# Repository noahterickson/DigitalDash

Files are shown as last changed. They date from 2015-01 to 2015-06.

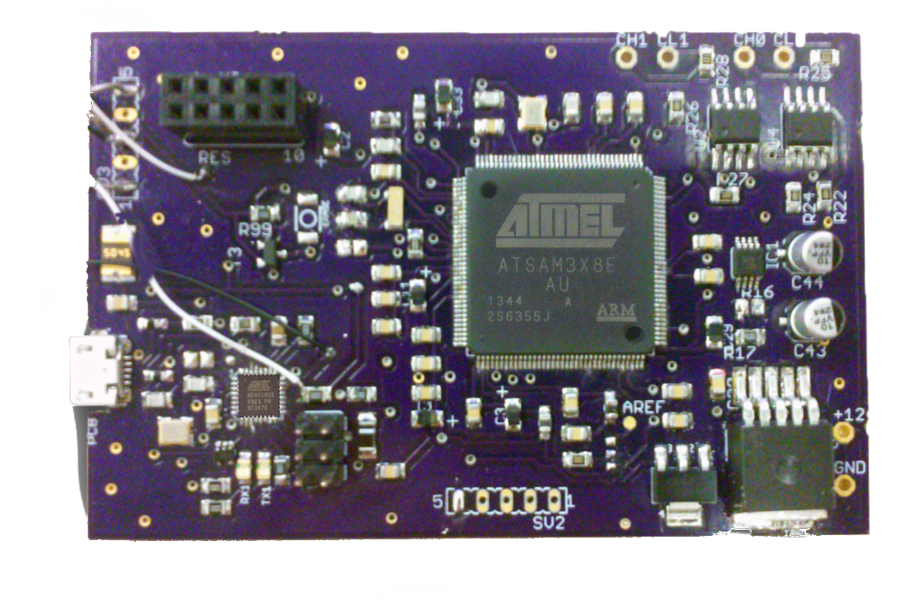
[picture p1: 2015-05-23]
images/Poster/custom.tiff

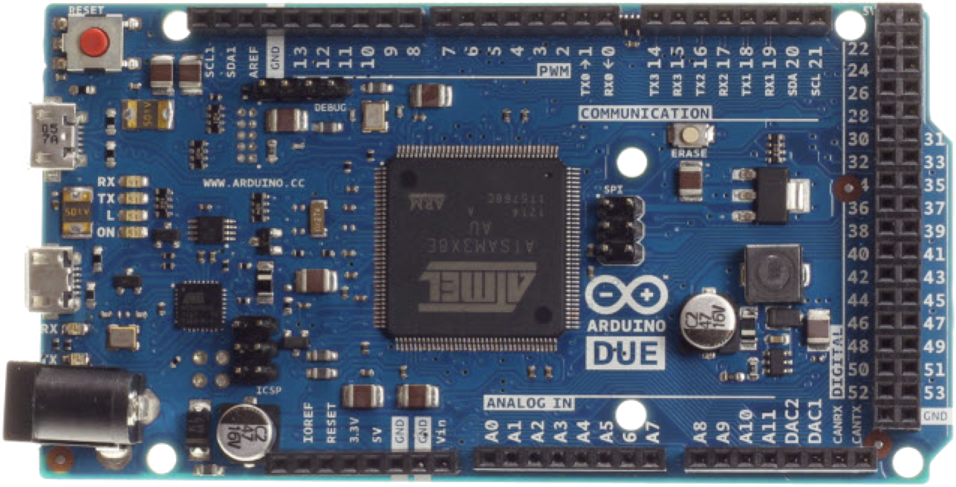
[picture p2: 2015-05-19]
images/Poster/arduino.tiff

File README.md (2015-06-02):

# Digital Dashboard

The digital dashboard project was completed by a group of students at Portland State University for the Electrical and Computer Engineering Capstone program on behalf of the Viking Motorsports team.

The digital dashboard is intended for a Formula SAE electric vehicle and functions as a visual display of information for various systems on the vehicle.

[Check out our wiki](https://github.com/noahterickson/DigitalDash/wiki)

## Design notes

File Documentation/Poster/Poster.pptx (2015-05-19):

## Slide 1

Digital Dash for SAE Electric Race Car
Capstone Team: Noah Erickson, Chad Thueson, Rishal Dass, Jaime Rodriguez, Sean Koppenhafer
Project Sponsor: Michal Podhrasky – Viking Motorsports Team
Capstone Advisor: Dr. Christof Teuscher – Portland State University ECE Department

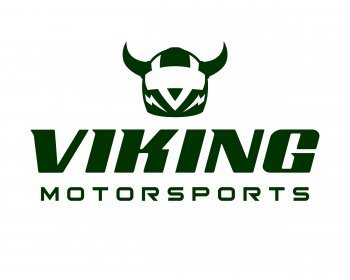
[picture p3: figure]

Prior Work

In the realm of racing each car is designed completely different based on several factors not limited to driver preferences, resources available and technical limitations. A few popular choices for digital dashboards currently exist. The popular Haltech Racepak is not only expensive, but requires the use of Haltech’s standalone ECU to source the data for the dash. Another setup would be a bluetooth adaptor plugged in to an OBDII port on board the car, but would’ve required the use of the OBDII protocol throughout the design of the car.

Implementation

CAN Transceivers

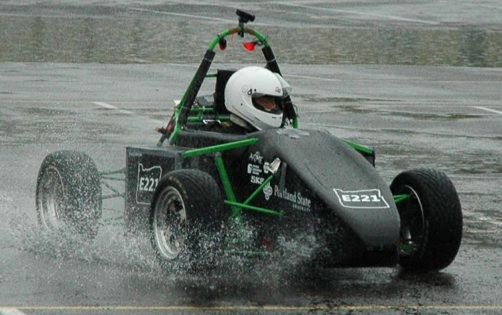
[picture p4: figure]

Microprocessor

Picture of whole unit here

Screen

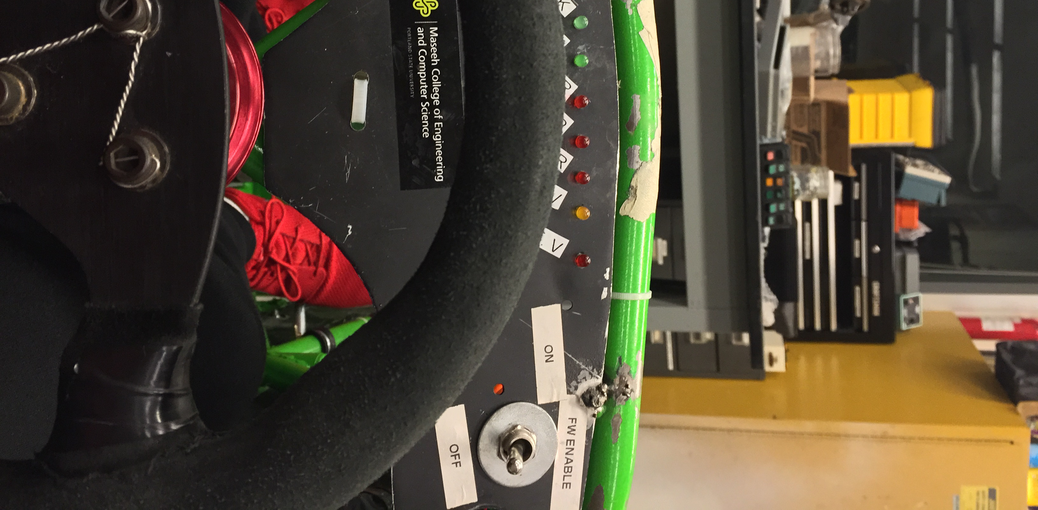
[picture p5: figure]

The software portion of the digital dash was created using the Arduino IDE. In order to interface with the CAN bus and the 4D systems screen the use of two separate Arduino libraries were used. The software sniffs the CAN bus looking for pertinent CAN messages and scales them to their correct values and sends the data to the screen.

The 4D Systems screen came with a useful piece of software to aide the quick creation of GUIs. The screen receives values from the mainboard through a serial connection. The GUI was created to be simple and intuitive. The designed GUI also utilizes the resistive touch capability of the screen in order to flip through a couple different submenus that include further information that a driver might want.

Performance

Oh yeah, it performs.

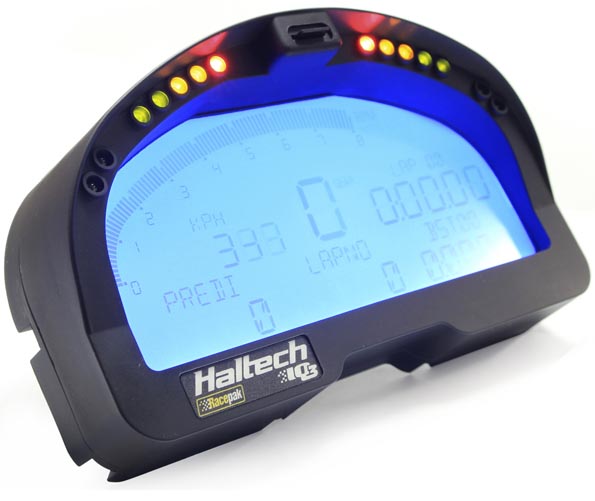
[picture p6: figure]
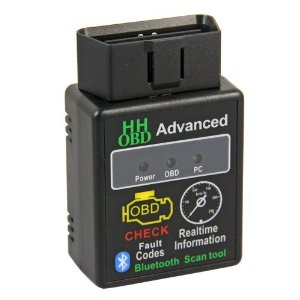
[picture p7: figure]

Hardware

The real estate that the digital dash unit took up on the physical dash needed to be minimal. This requirement dictated two large design choices:
- The 3.5” Display Size
- The custom PCB to cut down size

The entire system was first prototyped using an Arduino Due which was slightly too large for the solution we had in mind.

The screen was slightly smaller than the LCD and the Arduino Due would have a lot of wires plugging into the screen. We wanted our device to be as plug-and-play as possible so we created a custom PCB that would plug directly into the LCD with no “mod wires”.

Software

Screen

Motivation

The increased complexity that high voltage systems introduce onto a racecar require increased diagnostics to keep the car running safely. The Viking Motorsports team had previously used a simple bank of LEDs to indicate problems with mission critical systems. Troubleshooting these problems required the car to be off the track and logged data to be analyzed. With the addition of a digital dash system that reads data in real time from the vehicle control unit the driver could be kept up to date on system functionality either on track or in the pit stop.

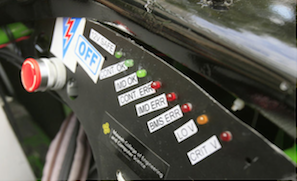
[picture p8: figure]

Picture of LCD screen on Car goes here!!

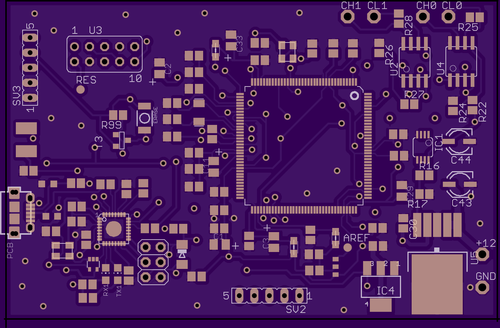
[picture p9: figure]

Further Improvements

- The digital dash could be implemented on the internal combustion car
- Screen size could be maximized to fit the vehicles dash
- The mainboard could be reprinted with the changes made, this would cut down on mod wires, cut traces and test connections
- An improved power supply could be implemented to cut down on power consumption and compatability with a 12V system.
- The enclosure could incorporate a cowl in order to improve readability in direct sunlight

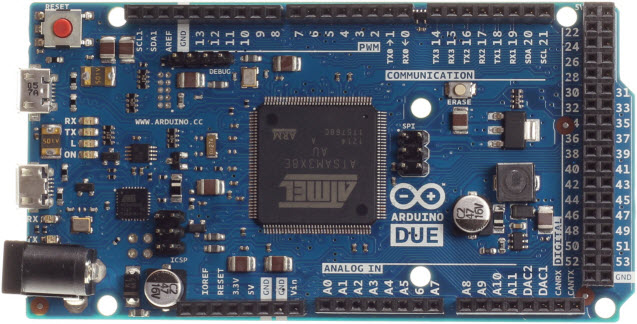
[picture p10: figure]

When it comes to implementing a digital dashboard on a Formula SAE racecar there are three major concerns. The first two concerns are solved by choosing a microprocessor, which was one of the first items we decided on. The microprocessor that drives the digital dashboard must support multiple communications protocols, in this case CAN and serial, and must be fast enough to handle receiving messages on a CAN bus. The 32bit 84MHz ATSAM3X microprocessor, the same microprocessor the Arduino Due uses, fit the bill perfectly with out of the box CAN capability. In addition to the microprocessors fast speeds and CAN capability, the design team could use an Arduino Due as an early prototyping platform while simultaneously designing a custom circuit board to house the ATSAM3X. Another large decision was the screen used since needed to have a high resolution while having a compact size. The high resolution is necessary to draw gauges, icons and bars all on the screen at once while the compact size is required by the layout of the vehicles frame.

Solution

Conclusions

This is objectively the best
digital dash ever created

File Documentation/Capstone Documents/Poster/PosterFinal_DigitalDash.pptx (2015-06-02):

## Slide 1

Digital Dashboard for Formula SAE Electric Racecar
Capstone Team: Noah Erickson, Chad Thueson, Rishal Dass, Jaime Rodriguez, Sean Koppenhafer
Project Sponsor: Michal Podhradsky – Viking Motorsports Team
Capstone Advisor: Dr. Christof Teuscher – Portland State University ECE Department

Acknowledgements: Michal Podhradsky, Dr. Christof Teuscher, Quinn Sullivan and the entire Viking Motorsports Team

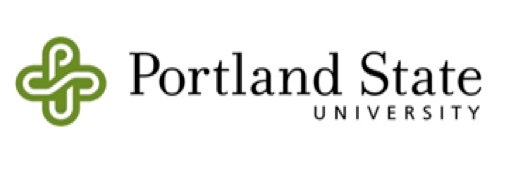
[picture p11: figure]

Abstract

The Viking Motorsports Electrical Vehicle (Figure 1) uses an array of LEDs to indicate problems with mission critical systems. (Figure 2) The increased complexity that high voltage systems introduce into a racecar require increased diagnostics to keep the car running safely and correctly. The driver must have the status of all important subsystems visible to clearly see and determine the vital faults, so they can adjust their driving style as necessary. With an updated dash system detailed information can be displayed in real time from the vehicle control unit. The driver can be kept up to date on system functionality both on track or in the pits.
The solution to display all this critical information is a small 3.5” LCD screen that will receive information from the subsystems of the vehicle and display them in a simple Graphical User Interface. The interface will not only display the warnings and faults like the old LED implementation but will also display useful real time information such as motor torque, battery level and amperage draw of the motor.

Implementation

Figure 4: Digital Dash Block Diagram

Software

The software for the Digital Dashboard was written in the Arduino IDE using the C programming language. In order to interface with the vehicles CAN networks and the 4D systems screen, two libraries provided by the respective distributers were used. The software receives data from the vehicles CAN networks by looking for pertinent messages. Then the messages are interpreted and sent to the screen.

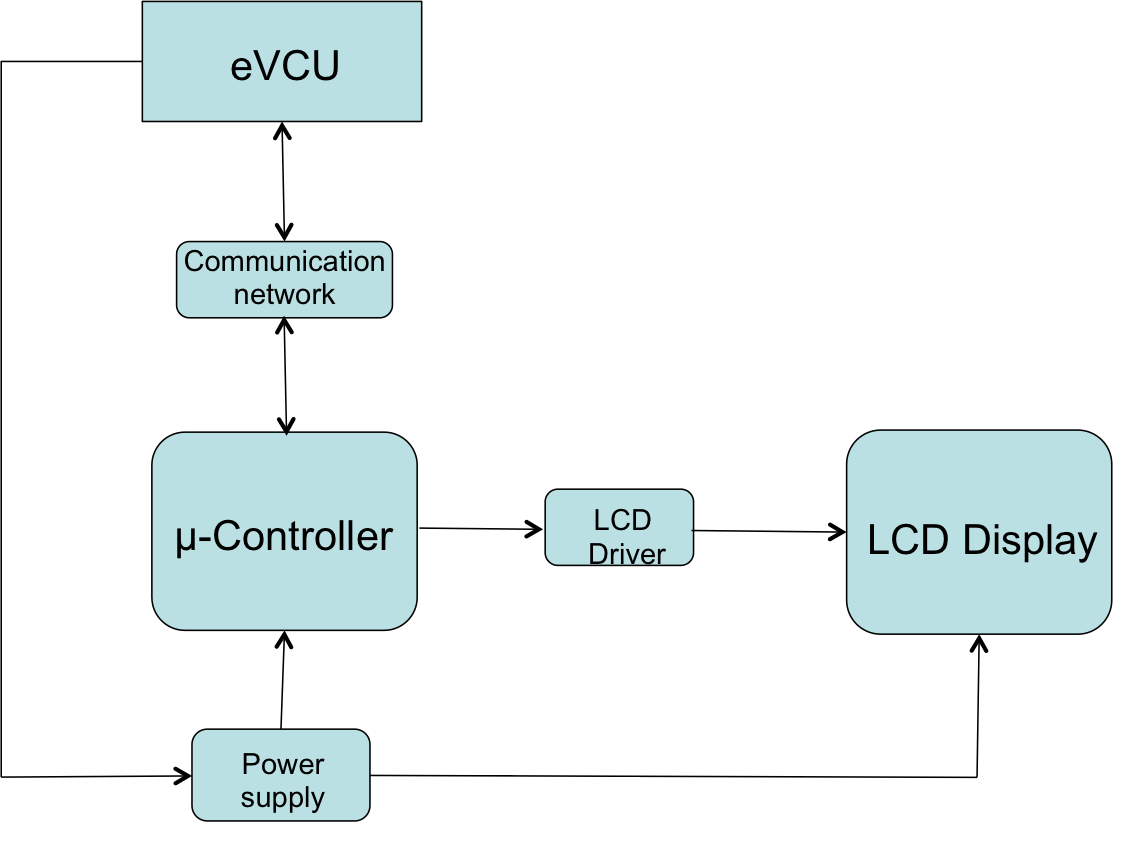
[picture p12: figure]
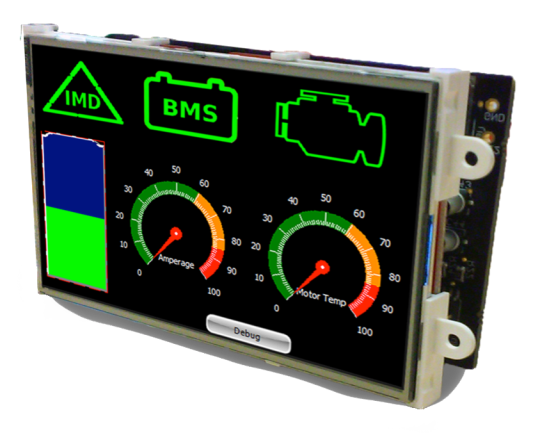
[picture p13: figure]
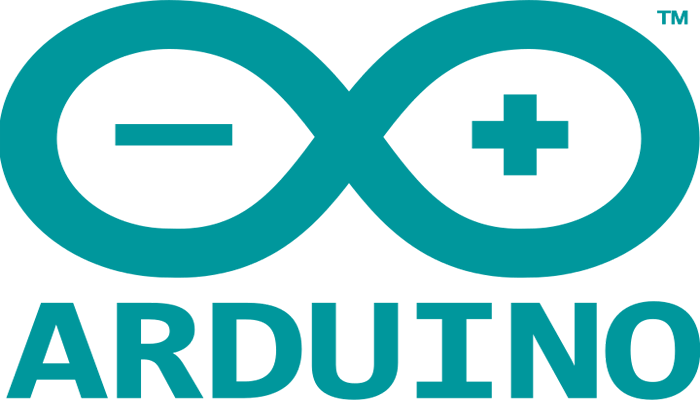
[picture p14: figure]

CAN Network

Programming Circuit

LCD Mating
Header


CAN Inputs

12V Supply

Figure 5: Custom PCB

Testing

For half of the development cycle we were able to use last years car as a test platform. During this time we were able to determine that messages from one of the two CAN networks were successfully being received and interpreted.
In the second half of the development cycle we did not have access to a functioning test vehicle. To determine if the digital dashboard worked, we developed a demo program to send out simulated messages that behaved similarly to the vehicles subsystems.


Figure 1: VMS SAE Electric Vehicle


Figure 2: Current Dash of Electric Vehicle

Hardware

A custom PCB was fabricated to fit in the limited space allocated for the dash in the vehicle. The layout of the board was designed so the control pins of the LCD would connect directly with the header affixed on the board. Our board was created by modifying the existing Arduino Due design. (Figure 5)

LCD DISPLAY

System
Micro Controller

CAN
Network

eVCU
Simulator

Data Input
Controller

Figure 7: Block Diagram for Demo System

Introduction to CAN

The Controller Area Network (CAN) bus is one of several central networking protocols that are used in the automotive industry. Implementing the CAN protocol allows the vehicles subsystems to communicate between each other.

Figure 3: CAN Network Example

The 3.5” screen is touch enabled. It gives us the capability to navigate through multiple screens by way of on screen buttons to view data from different systems. This allows the user to view more detailed information about the vehicles’ respective subsystems. The screen layout was kept as simple as possible to allow the driver to quickly glance at the screen and interpret the data.(Figure 6)

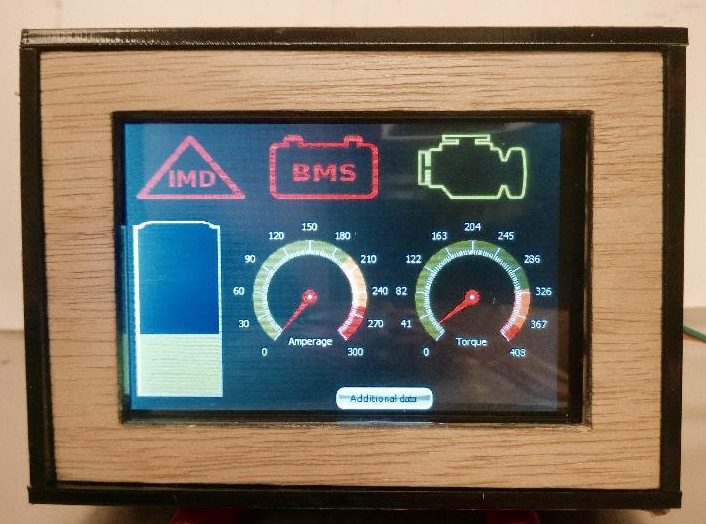
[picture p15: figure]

Figure 6: LCD Displaying Main Screen

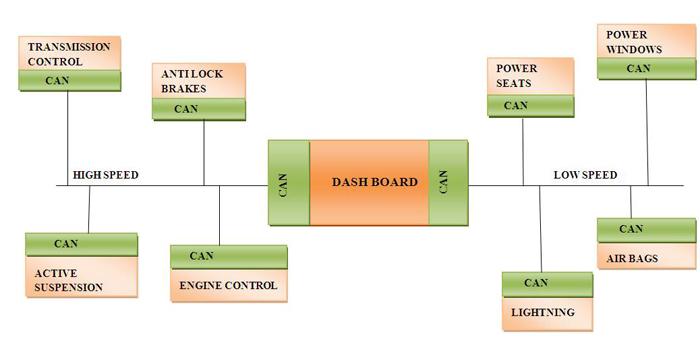
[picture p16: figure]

Conclusion

The digital dashboard performs as intended when simulated with the demo program that we created. Instead of testing all functionally of the screen, the demo program focuses on only the most important functions.
Due to circumstances outside of our control, the digital dashboard has not been officially tested on the electric vehicle but we are confident that it would function correctly.

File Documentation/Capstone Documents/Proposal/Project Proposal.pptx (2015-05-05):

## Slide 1

Sean Koppenhafer, Jaime Rodriguez,
Chad Thueson, Noah Erickson, Rishal Dass

Project Proposal

Digital Dash

Portland State University

Department of Electrical and Computer Engineering (ECE)

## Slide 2

Overview

- Project Overview & Requirements
- Devices Chosen
  - Microcontroller
  - CAN Transceiver
  - LCD Screen
- GUI Layout
- Enclosure
- Budget
- Project Timeline

## Project Overview

- Electric systems add complexity and a traditional LED dash won't suffice
- Drivers must be aware of system faults and warnings
- An LCD Dashboard must be created to accommodate additional electrical systems

Formula SAE Electric Car

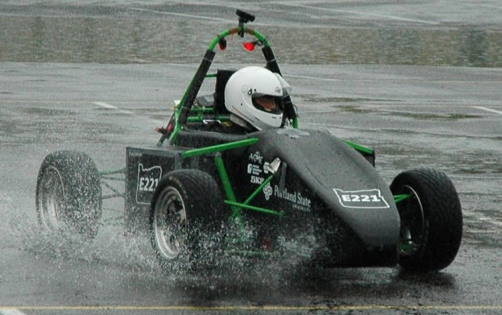
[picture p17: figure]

Current Traditional LED Dash

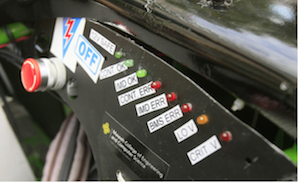
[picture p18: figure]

## Project Requirements

- Budget: $500
- Timeline: March 2015
- The display gather information from the CAN-bus and display it in a simple LCD GUI
- Deliverables
  - One functional Unit
  - Well Documented Code
  - Professional Documentation
  - User Manual

## Design Constraints

- Choose most suitable LCD display
- Design the communication interface with VCU
- Develop GUI
- Design waterproof casing for the display
- Physical space on dash is limited

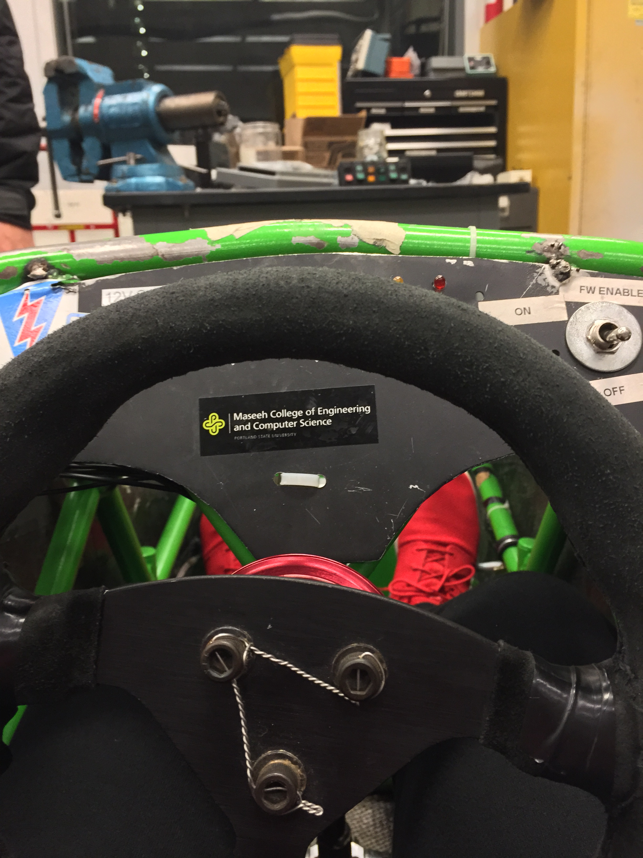
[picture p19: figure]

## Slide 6

Devices Chosen

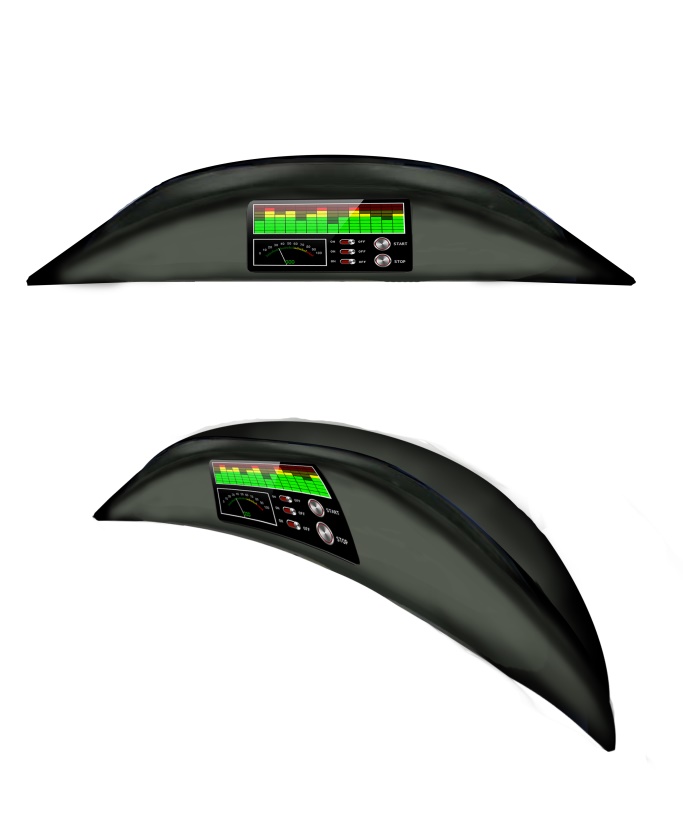
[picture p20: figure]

- CAN Protocol for data acquisition with serial to LCD
- AT90CAN Atmel
- AMS-42700 On Semiconductor
- uLCD-35DT 4D systems

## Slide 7

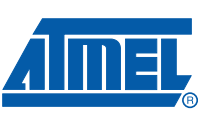
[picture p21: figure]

Microcontrollers

| Cost | Fab Board | CAN Controller | CAN Library | SPI, I2C, UART, etc
Atmega 328 | ~$3 | Yes | No | No | Yes
AT90CAN | ~$8 | Yes | Yes | Yes | Yes
Arduino Uno | ~$25 | No | No | No | Yes
Arduino Due | ~$50 | No | Yes | No | Yes

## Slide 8

CAN Transceiver

| Cost | Max Transfer Rate | Multiple CAN networks
AMIS-42700 | ~$6 | 1 Mbit/sec | Yes (2 networks)
MCP-2551 | ~$1.50 | 1 Mbit/sec | No (1 network)

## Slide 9

Reasons for Choices

- CAN is the standard for vehicle communication
- Low message transfer latency
- Simplicity to implement and expand
- Other options
  - Serial
  - Wireless
  - USB

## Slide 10

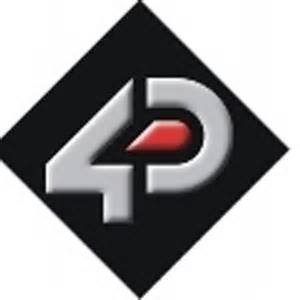
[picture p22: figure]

LCD Screen

2.7” LCD display
3.5” LCD display
4.7” LCD display (too large)
- Pros
  - Resistive Touch
  - Color display
  - Power Graphics processor
  - Simple tools to create Gui
  - High Resolution
- Cons
  - Screen is not polarized, difficult to see in sunlight (shield can be bought)
P/N uLCD-35DT

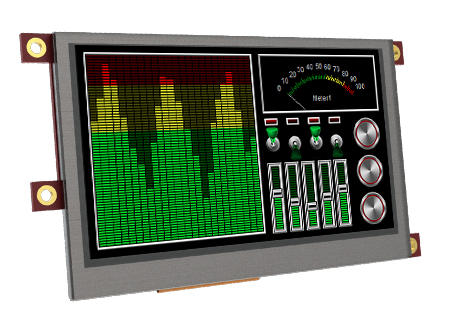
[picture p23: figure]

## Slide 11

GUI Layout

Flashing warnings symbols will indicate errors in BMS, and IMD System.

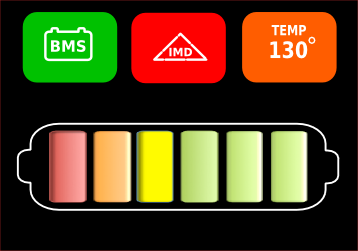
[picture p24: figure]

Proposed - Display GUI Layout (basic)

Temperature indicator for motor or controller.

Battery meter will indicate voltages between safe and critical levels.

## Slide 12

GUI Layout

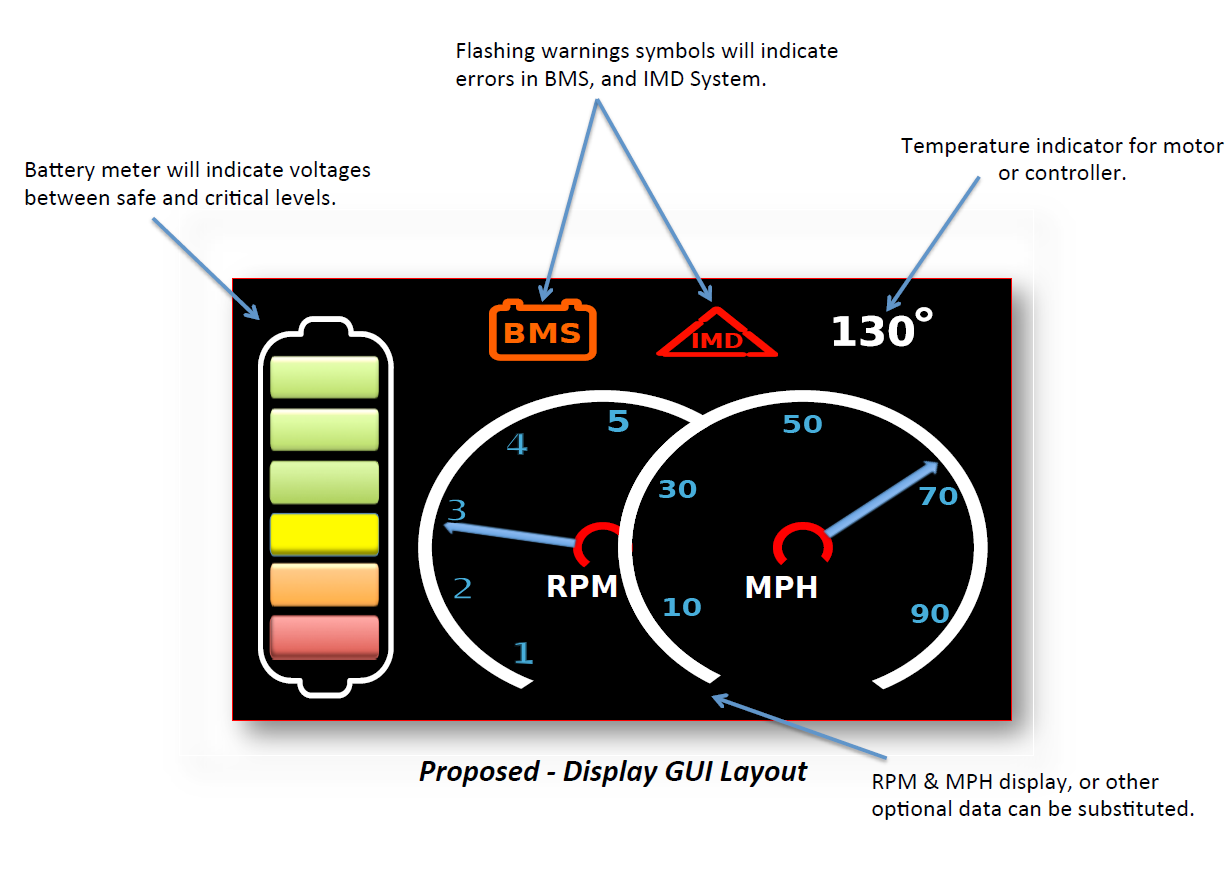
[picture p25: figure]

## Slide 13

Enclosure

On top of dash
- Pros
  - Looks good
- Cons
  - 3D Printed (expensive)
  - Sticks out of cockpit (rule violation?)
In Dash
- Pros
  - Looks good
  - Waterproof
- Cons
  - 3D Printed (expensive)
  - Limited View

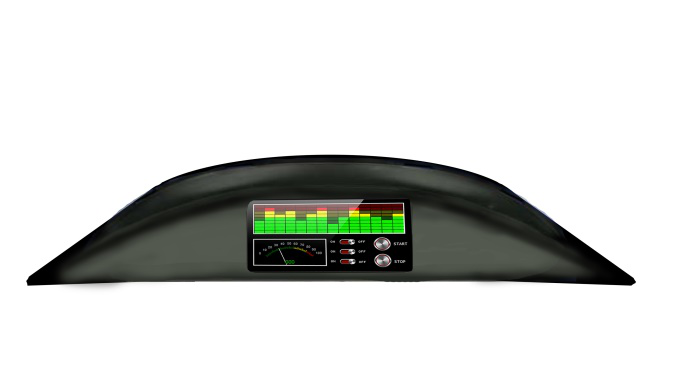
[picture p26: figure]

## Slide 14

Budget

- AT90CAN ~$10, plus ~$20 for board FAB
- 4D 3.5" Screen ~$150 for screen & shield
- Deutsch Connectors ~$10
- Enclosure ~$50
- $250 for one system

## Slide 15

Project Timeline


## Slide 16

Questions & Concerns?

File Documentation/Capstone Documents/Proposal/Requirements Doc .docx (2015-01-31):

Requirements

Constraints

The LCD display must be readable in all weather conditions. A trans-reflective display that is 500-900 nits bright will allow the display to be readable in sunlight. A waterproof enclosure will allow the device to operate in rainy conditions and allow it to be readable in rain. The digital dash unit must be large enough to be readable but small enough to be mountable on the dash of the electric car. A 3.5” LCD screen will allow for both size constraints.

Objective

The digital dash will give the operator of the electric car critical system warnings of various systems. The warnings will come from a CAN bus connected from the electric car VCU that will be connected to a microcontroller contained in the digital dash unit. The microcontroller will parse the CAN data and display it on the LCD contained in the digital dash unit. The microcontroller, LCD and a power supply will be contained in a waterproof enclosure that is easily installable on to the current setup of the Formula SAE electric car.

# Engineering Requirements

Operation

- The unit must have a trans-reflective screen capable of 500-900 nits, for visibility in direct sunlight.
- The digital dash should gather data from the EVCU, BMS and Motor controller and be able to interpret data and display in a graphical interface.
- The display’s interface must be simple and clear so driver can easily read at a quick glance; it should include big fonts and symbols with bright colors to differentiate indicators.
- Displayed data does not need to be real-time, but update and refresh at a rate that will be useful.
- The electric car must be independent of display system and run with or without it, in case of failure the electric car must still be operable.
- Display must boot up in less than 30 seconds, so it is not a nuisance to turn on and use.

### Power

- Display must be able to be powered by a 12V DC supply, the unit will be powered from the main battery on the electric car.
- A power supply must be designed for the digital dash to be robust against electrical noise. And be able to regulate battery voltage (9-13V) down to the display and controller voltage of 5V.

### Health & Safety

- Display must be securely bolted to car frame and not stick out of car body to prevent module from flying of and injuring driver.

### Environmental

- Must be made with non-toxic/hazardous chemicals that would require proper disposal.

### Maintainability

- Must have minimal to no user maintenance over entire life cycle.

### Dimensions

- There are constraints to the size of the screen, the electric car dash does not have a lot of space available in the drivers cab so display must be restricted to max of a 4” diagonally, and must have a clear line of sight.

### Reliability & Availability

- The display must rugged and water resistant (IP65 standard) as will be exposed to wet weather conditions.
- The display must be easily made to install and detach to various racecar frames.

### Price

- Total parts and manufacturing should not exceed $500 as to accommodate the Viking Motorsport budget. The digital dash must also be relatively cheap to be a viable open source alternative to similar existing solutions.

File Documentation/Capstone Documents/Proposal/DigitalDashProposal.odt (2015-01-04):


Figure 1: Current LED Indicators

Viking Motorsports

Digital Dash

Project Proposal

January 3rd, 2015

Sean Koppenhoffer, Rishal Dass

Jaime Rodriquez, Noah Erickson, Chad Thueson

Objective

The objective of this unit is to provide the operator of the Viking Motorsports Formula SAE electric vehicle with information about the vehicles operation. The information will be gathered from the onboard VCU, deciphered by a main processing unit and displayed on an LCD mounted in the operators view. Mission critical information, such as warnings about battery temperatures, will be displayed on the digital dash.

Motivation

The current system used to warn operators of warning messages is with a simple LED indicator. This results in an array of many LEDs with corresponding labels cluttering up the dash board of the Formula SAE vehicle. The LED indicators on the current Formula SAE electric car can be seen in figure 1. By switching over to a digital dash the LED indicators along with their wires can be removed and the information consolidated into a single system that is easy to manage.

Description

The complete package will be made up of a single enclosed unit. The unit will contain a power supply for the microcontroller and LCD screen, a microcontroller that interprets data from the VCU, and an LCD screen that displays the relevant information. The digital dash unit will have a trans-reflective screen allowing it to be read in sunlight. The unit will also be designed to be small, waterproof and robust.

Components

The microcontroller that will be used is the AT90CAN. The LCD that will be used is the uLCD-35DT-AR from 4Dsystems.


Figure 2: Proposed Digital Dash

μ-Controller Communication network LCD Driver LCD Display Power supply eVCU Figure 3: Block Diagram

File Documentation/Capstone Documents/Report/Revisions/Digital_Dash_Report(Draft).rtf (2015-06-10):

Portland State University

Viking Motorsports

ECE Capstone 2014

Digital Dashboard

Noah Erickson

Rishal Dass

Chad Thueson

Jaime Rodriguez

Sean Koppenhafer

www.github.com/noahterickson/digitaldash

Abstract

Nulla malesuada porttitor diam. Donec felis erat, congue non, volutpat at, tincidunt tristique, libero. Vivamus viverra fermentum felis. Donec non-ummy pellentesque ante. Phasellus adipiscing semper elit. Proin fermentum massa ac quam. Sed diam turpis, molestie vitae, placerat a, molestie nec, leo. Maecenas lacinia. Nam ipsum ligula, eleifend at, accumsan nec, sus-cipit a, ipsum. Morbi blandit ligula feugiat magna. Nunc eleifend consequat lorem. Sed lacinia nulla vitae enim. Pellentesque tincidunt purus vel magna. Integer non enim. Praesent euismod nunc eu purus. Donec bibendum quam in tellus. Nullam cursus pulvinar lectus. Donec et mi. Nam vulputate metus eu enim. Vestibulum pellentesque felis eu massa.

Contents

1 Introduction | 3
1.1 Purpose . . . . . . . . . . . . . . . . . . . . . . . . . . . . . . . . . | 3

1.2 Motivation . . . . . . . . . . . . . . . . . . . . . . . . . . . . . . . . 3 1.2.1 Vehicle Complexity . . . . . . . . . . . . . . . . . . . . . . . 3

1.2.2 Setting a Standard . . . . . . . . . . . . . . . . . . . . . . . | 4
2 Problem Statement | 4

2.1 Project Requirements . . . . . . . . . . . . . . . . . . . . . . . . . . 5 2.1.1 Operation . . . . . . . . . . . . . . . . . . . . . . . . . . . . 5

2.1.2 Power . . . . . . . . . . . . . . . . . . . . . . . . . . . . . . 5

2.1.3 Health & Safety . . . . . . . . . . . . . . . . . . . . . . . . . 5

2.1.4 Environmental . . . . . . . . . . . . . . . . . . . . . . . . . 6

2.1.5 Maintainability . . . . . . . . . . . . . . . . . . . . . . . . . 6

2.1.6 Dimensions . . . . . . . . . . . . . . . . . . . . . . . . . . . 6

2.1.7 Reliability & Availability . . . . . . . . . . . . . . . . . . . . 6

2.1.8 Price . . . . . . . . . . . . . . . . . . . . . . . . . . . . . . . 6

3 Solution Space | 6

3.1 Mainboard . . . . . . . . . . . . . . . . . . . . . . . . . . . . . . . . 7

3.1.1 Micro-controller . . . . . . . . . . . . . . . . . . . . . . . . . 7

3.1.2 CAN Transceivers . . . . . . . . . . . . . . . . . . . . . . . . 8

3.1.3 LCD Screen . . . . . . . . . . . . . . . . . . . . . . . . . . . 9

3.2 Power Supply . . . . . . . . . . . . . . . . . . . . . . . . . . . . . . 9

3.3 Software . . . . . . . . . . . . . . . . . . . . . . . . . . . . . . . . . 9

3.4 Display . . . . . . . . . . . . . . . . . . . . . . . . . . . . . . . . . . | 9

3.5 Graphical User Interface . . . . . . . . . . . . . . . . . . . . . . . . 10

3.6 Enclosure . . . . . . . . . . . . . . . . . . . . . . . . . . . . . . . . 10

3.7 Communication Protocol . . . . . . . . . . . . . . . . . . . . . . . . 10

4 Implementation | 11

4.1 Software . . . . . . . . . . . . . . . . . . . . . . . . . . . . . . . . . 11

1

5 Explanations | 11

5.1 Protocols Utilized . . . . . . . . . . . . . . . . . . . . . . . . . . . . 11

5.1.1 CAN Bus . . . . . . . . . . . . . . . . . . . . . . . . . . . . 11

5.1.2 Serial . . . . . . . . . . . . . . . . . . . . . . . . . . . . . . . 12

5.2 Tools Used . . . . . . . . . . . . . . . . . . . . . . . . . . . . . . . . 12

5.2.1 | Arduino IDE . . . . . . . . . . . . . . . . . . . . . . . . . . | 12
5.2.2 | Eagle CAD . . . . . . . . . . . . . . . . . . . . . . . . . . . | 12
5.2.3 | 4DSystems Visi-Genie . . . . . . . . . . . . . . . . . . . . . | 12
5.2.4 | Hardware tools . . . . . . . . . . . . . . . . . . . . . . . . . | 12
6 Testing | | 13
6.1 Testing Objectives . . . . . . . . . . . . . . . . . . . . . . . . . . . | 13

6.1.1 Testing Purpose . . . . . . . . . . . . . . . . . . . . . . . . . 13

6.1.2 Testing Scope . . . . . . . . . . . . . . . . . . . . . . . . . . 13

6.2 Requirements for Test . . . . . . . . . . . . . . . . . . . . . . . . . | 14
6.2.1 | Function Testing . . . . . . . . . . . . . . . . . . . . . . . . | 14
6.2.2 | User Interface Testing . . . . . . . . . . . . . . . . . . . . . | 14
6.2.3 | Performance Testing . . . . . . . . . . . . . . . . . . . . . . | 15

6.2.4 Load testing . . . . . . . . . . . . . . . . . . . . . . . . . . . 15

6.2.5 Stress Testing . . . . . . . . . . . . . . . . . . . . . . . . . . 15

6.2.6 Ruggedized Testing . . . . . . . . . . . . . . . . . . . . . . . 15

6.3 Test Strategy . . . . . . . . . . . . . . . . . . . . . . . . . . . . . . | 16
6.3.1 | Function Testing . . . . . . . . . . . . . . . . . . . . . . . . | 16
6.3.2 | User Interface Testing . . . . . . . . . . . . . . . . . . . . . | 16
6.3.3 | Performance Testing . . . . . . . . . . . . . . . . . . . . . . | 17

6.3.4 Stress Testing . . . . . . . . . . . . . . . . . . . . . . . . . . 18

6.3.5 Load Testing . . . . . . . . . . . . . . . . . . . . . . . . . . 18

6.3.6 Ruggedness Testing . . . . . . . . . . . . . . . . . . . . . . . 18

6.4 Testing Equipment . . . . . . . . . . . . . . . . . . . . . . . . . . . 19

6.5 Resources . . . . . . . . . . . . . . . . . . . . . . . . . . . . . . . . 19

6.6 Results . . . . . . . . . . . . . . . . . . . . . . . . . . . . . . . . . . 19

7 | Conclusion | 20
8 | LICENSING INFORMATION | 20

2

1 Introduction

1.1 Purpose

The objective of this unit is to provide the operator of the Viking Motorsports Formula SAE electric vehicle with information about the vehicles operation. The information will be gathered from the on-board vehicle control unit (VCU), deciphered by a main processing unit and displayed on a liquid crystal display (LCD) mounted in the operators view. Mission critical information, such as warnings about battery management systems (BMS), insulation-monitoring devices (IMD) and system temperatures will be displayed on the digital dash.

1.2 Motivation

With the current set-up on the electric vehicle, it using Light Emitting Diodes (LED) that lights up when it detects an error. Although this works, it would be more productive for the driver to know what more information that is causing the error. For example, during a race if the battery is running low, it would be more e cient for the driver to know exactly how much battery life is left rather than know that the battery is low. With this extra bit of data it would be more helpful of the driver to decide if he/she can make it another lap or if they need to make a pit stop.

1.2.1 Vehicle Complexity

The Viking Motorsports team has an internal combustion engine vehicle for Formula SAE races and their new electric car intended for the same purpose was modeled closely to it. With the addition of complex electrical systems it is the desire of the Viking Motorsports team to have this re ected in the aesthetics of the vehicle. The digital dash will integrate with the vehicles systems to display relevant information to the driver and will look good doing so.

3

Figure 1: Traditional LED Dashboard

1.2.2 Setting a Standard

Another motivation for the digital dash is to guide the future of electric cars created for the purpose of Formula SAE. The Viking Motorsports team would like to have the digital dash be open source so they can share it with other teams that are interested. Perhaps if enough teams adapt to a digital dash the product can evolve over time to support new features outside the scope of this proposal.

Currently the Formula SAE rules require a row of LEDs on the dashboard of any competing electric car.(SOURCE) The LEDs display information about system voltage and IMD status. If the digital dash can be built in such a way that it displays this information constantly and reliably perhaps the LEDs can be removed and the digital dash could be the new standard.

2 Problem Statement

The LCD display must be readable in all weather conditions. A trans-re ective display that is 500-900 nits bright will allow the display to be readable in sunlight. A waterproof enclosure will allow the device to operate in rainy conditions and allow it to be readable in rain. The digital dash unit must be

4

large enough to be readable but small enough to be mountable on the dash of the electric car. A 3.5 LCD screen will allow for both size constraints.

2.1 Project Requirements

2.1.1 Operation

The unit must have a trans-re ective screen capable of 500-900 nits, for visibility in direct sunlight.

The digital dash should gather data from the EVCU, BMS and Motor controller and be able to interpret data and display in a graphical interface.

The displays interface must be simple and clear so driver can easily read at a quick glance; it should include big fonts and symbols with bright colors to di erentiate indicators.

Displayed data does not need to be real-time, but update and refresh at a rate that will be useful.

The electric car must be independent of display system and run with or without it, in case of failure the electric car must still be operable.

Display must boot up in less than 30 seconds, so it is not a nuisance to turn on and use.

2.1.2 Power

The display must be able to be powered by a 12V DC supply, the unit will be powered from the main battery on the electric car.

A power supply must be designed for the digital dash to be robust against electrical noise and be able to regulate battery voltage (9-13V) down to the display and controller voltage of 5V.

2.1.3 Health & Safety

Display must be securely bolted to car frame and not stick out of car body to prevent module from ying of and injuring driver.

5

2.1.4 Environmental

Must be made with non-toxic/hazardous chemicals that would require proper disposal.

2.1.5 Maintainability

Must have minimal to no user maintenance over entire life cycle.

2.1.6 Dimensions

There are constraints to the size of the screen, the electric car dash does not have a lot of space available in the drivers cab so display must be restricted to max of a 4 diagonally, and must have a clear line of sight.

2.1.7 Reliability & Availability

The display must rugged and water resistant (IP65 standard) as will be exposed to wet weather conditions.

The display must be easily made to install and detach to various racecar frames.

2.1.8 Price

Total parts and manufacturing should not exceed $500 as to accommodate the Viking Motorsport budget.

The digital dash must also be relatively cheap to be a viable open source alternative to similar existing solutions.

3 Solution Space

The digital dash unit will have two inputs and one output. The unit will have two CAN transceivers that take one CAN bus input each, one for the battery management system (BMS) bus and one for the RMS bus. The digital dash will process these inputs and output pertinent information to an LCD.

6

Figure 2: Functional Block Diagram

3.1 Mainboard

The mainboard is functionally a custom Arduino Due that has been reduced in size to the necessary components for the digital dash. The mainboard is a printed circuit board from OSH Park that includes a power supply and two CAN transceivers in addition to the Arduino Due architecture.

3.1.1 Micro-controller

After researching the many micro-controller that could be used the choice came down to four; Atmega328, AT90CAN, Arduino UNO, and Arduino Due. These four (4) micro-controllers that have the capabilities and would be possible to integrate the current system with the new one.

Atmega328:

AT90CAN:

Arduino UNO:

We decided to go with the Arduino Due because the system that is being using

7

with the Viking Motor Sport team was a custom made Arduino Due board, so using another Due would make the integration with there system much easier and cost e ective. The open-source electronic prototyping platform, Arduino, was the inspiration for the mainboard. The Arduino Due has an ATSAM3X Atmel micro-controller on it that has CAN capability. The ATSAM3X is a 32-bit, 84-MHz micro-controller that will operate quick enough to handle the messages being transmitted on the CAN bus. The ATSAM3X will acquire the messages sent across the two CAN buses through two CAN transceivers and decide what information is needed to be displayed on the dash.

The main choice for the ATSAM3X was its performance capabilities to keep up with the capacity of messages on the CAN bus. Additionally, the Viking Motorsports Team also uses an Arduino Due, with an ATSAM3X microcontroller, in their eVCU. Basing the digital dash o the Arduino Due helps with compatability issues with the current systems onboard the car.

By using the ATSAM3X the development team was able to quickly prototype the digital dash unit using an Arduino Due which was another major factor in choosing the micro-controller.

| Cost | Fab Board | CAN Controller | CAN Library | SPI, I2C, UART
Atmega328 | $3 | Yes | No | No | Yes
AT90CAN | $8 | Yes | Yes | Yes | Yes
Arduino UNO | $25 | No | No | No | Yes
Arduino Due | $50 | No | Yes | Yes | Yes

Table 1: Micro-controller Choices

3.1.2 CAN Transceivers

Two MCP2551 CAN transceivers were chosen for integrating the CAN buses. The main choice for this The CAN transceivers job is to merge two CAN buses together. The BMS and RMS CAN buses have di erent baud rates and cannot be simply connected to each other. The job of the CAN transceiver is to take the

8

two buses and merge them onto a single bus. The device comes in either a

through hole or surface mount package.

| Cost | Max Transfer Rate | Multiple CAN Networks
AMIS-42700 | $6 | 1 Mbit/sec | Yes (2 networks)
Arduino Due | $1:50 | 1 Mbit/sec | No (1 network)

Table 2: CAN Transceiver Choices

3.1.3 LCD Screen

3.2 Power Supply

The power supply was implemented using a TLF1936 voltage regulator and the necessary components to drive it. The power supply was designed to be used on either a 5 volt or 12 volt system for additional compatibility with other systems. For the Viking Motorsports Electric Vehicle we grabbed 12 volts from the on-board power supply.

3.3 Software

The software for the ATSAM3X was written in the Arduino IDE to provide compatibility and ease of use for further implementation by the Viking Motorsports Team.

3.4 Display

The display used is a 4D Systems uLCD-35DT-AR. It was chosen for its 3.5" size, compatibility with Arduino, its touchscreen capabilities and low cost. The display will output the information that is passed to it from the micro-controller and will be able to independently handle all the graphics processing to lessen the load of the ATSAM3X. A polarizing shield will be equipped to the display to help performance in direct

9

3.5 Graphical User Interface

The graphical user interface(GUI) uses a black background to minimize clutter and has three large icons in the upper portion indicating the insulation monitoring device (IMD) status, the BMS status and the RMS status. Under this there will be a battery meter, a battery amperage draw gauge and a motor torque gauge.

The GUI was designed with a minimalistic approach in order to reduce clutter and to give the digital dash a professional feel. In addition to the simple layout of the GUI each status icon has a sub-menu activated via the touchscreen that can show further information about a system. On the main screen of the GUI there is also a debug sub-menu that will show pertinent temperatures.

3.6 Enclosure

3.7 Communication Protocol

The GEVCU on-board the Viking Motorsports Electric Vehicle must have some integration with the digital dash unit in order to transmit data. There are a number of di erent protocols that are available to transfer data from the GEVCU to the digital dash unit. A few communication protocols the design team thought about using were: Wi-Fi, I2C, serial and CAN.

Since the GEVCU is Wi-Fi capable, this seems like an obvious choice in order to cut down on physical hardware. Implementing Wi-Fi into the digital dash unit would be simple as picking apart a Wi-Fi Arduino Shield and designing it to t the custom circuit board, once again cutting down on space. However, Wi-Fi was nixed early on as we thought this would over complicate the design process without much bene t to the project.

Another option would've been serial communication between the GeVCU and the digital dash unit. The ATSAM3X has quite a few serial communication options in the form of UARTs, SPI and CAN interfaces. The design team decided against using UART and SPI because the components on the electric vehicle communicate to the GEVCU using CAN buses.
Choosing CAN as our communication protocol with the GEVCU will allow the

10

design team to hijack data from the current CAN buses. This will allow the digital dash to see all the data that the GEVCU sees and not interfere with mission critical functions during races.

4 Implementation

4.1 Software

Software inplementation goes here

5 Explanations

Fusce mauris. Vestibulum luctus nibh at lectus. Sed bibendum, nulla a faucibus semper, leo velit ultricies tellus, ac venenatis arcu wisi vel nisl. Vestibulum diam. Aliquam pellentesque, augue quis sagittis posuere, turpis lacus congue quam, in hendrerit risus eros eget felis. Maecenas eget erat in sapien mattis porttitor. Vestibulum porttitor. Nulla facilisi. Sed a turpis eu lacus commodo facilisis. Morbi fringilla, wisi in dignissim interdum, justo lectus sagittis dui, et vehicula libero dui cursus dui. Mauris tempor ligula sed lacus. Duis cursus enim ut augue. Cras ac magna. Cras nulla. Nulla egestas. Curabitur a leo. Quisque egestas wisi eget nunc. Nam feugiat lacus vel est. Curabitur consectetuer.

5.1 Protocols Utilized

5.1.1 CAN Bus

The Controller Area Network or CAN bus is one of several central networking protocols that are used in vehicles that do not have a host computer. Companies are starting to move towards vehicles that are more technologically advanced and equally more environmental friendly. With these advances, all the individual working modules in the vehicle needs to be connected so that they can communicate with each other. For example, the engine reports the vehicles speed to the transmission, which in turn must tell other modules when to shift gears. To be able to connect all these di erent modules together to work e ciently and e ectively a central networking system becomes necessary.

11

Having all the modules connected together into one system has numerous bene ts. The most signi cant bene t is the price to performance ratio that it o ers. This makes the current CAN bus technology the most reliable and cost e ective choice for the automotive companies. If a major event occurs in one of the modules it is shown in the main controller and will allow the rest of the modules to take the proper actions. If one of the modules of the CAN bus happens to fail other modules are not a ected unless they are directly related to each other. Diagnostics of the vehicle using the CAN bus becomes easier as well. It can pinpoint what has cause the module to fail and x that module instead of tearing the whole vehicle apart.

5.1.2 Serial

We used serial to communicate with the display.

5.2 Tools Used

5.2.1 Arduino IDE

The Arduino IDE was used for the data acquisition of the CAN bus and the processing of that data. The data was input using CAN protocol and output to the LCD module using serial.

5.2.2 Eagle CAD

Eagle CAD was used to create the hardware schematic as well as the custom printed circuit board layout.

5.2.3 4DSystems Visi-Genie

The GUI portion of the LCD was created using 4D Systems Visi-Genie software. This IDE integrated nicely with the Arduino IDE with an external library.

5.2.4 Hardware tools

Creating the wiring harness needed some tools such as wire strippers, wire crimpers, multi-meters, oscilloscopes and soldering irons.

12

Creating the enclosure and the demonstration unit included using the laser cutter in the Electronics Prototyping Lab (EPL) at Portland State University. Creating the rst prototype PCB required the use of the LPKF PCB Router in the EPL.

Creating the nal PCB required the use of the re ow oven in the EPL as well as the surface mount soldering station.

6 Testing

6.1 Testing Objectives

6.1.1 Testing Purpose

The following test plan documentation supports the following objectives:

Identify existing project information and the software and hardware that should be tested.

List the recommended test requirements (high level).

Recommend and describe the testing strategies to be employed.

Identify the required resources and provide an estimate of the test e orts. List the deliverable elements of all tests.

6.1.2 Testing Scope

This test plan describes the integration and system tests that will be conducted on the Viking Motorsports digital dash following the integration of subsystems and components identi ed in the Design Considerations for prototyping document [1].

The purpose of this test plan is to test the feasibility and performance of the Digital Dash. It is critical that all subsystems be tested before integration into the system so as to ensure a proper user experience when using the digital dash is integrated into racing vehicle.

The following modules and interfaces will be tested:

13

CAN message interpretation Data transmission to LCD GUI on LCD screen
Critical performance measures to test are:

Minimal time to capture and interpret CAN data

Time to display data on LCD screen after data interpretation Initialization time before the digital dash is ready to use

6.2 Requirements for Test

The lists below identify items (functional requirements, non-functional requirements and use cases) that have been targeted for testing. This listing represents what will be tested.

6.2.1 Function Testing

Project Requirements: The system must be powered by a 12V source Data from CAN network is being relayed to Arduino Due for analysis Data from Arduino Due is being sent to LCD

Data is being properly interpreted and displayed in GUI on LCD

6.2.2 User Interface Testing

LCD Screen must be viewable in sunlight

Project Requirements: "The digital dash should be easily readable, big fonts, non-cluttered display."

The following variables must be displayed on the LCD screen { Main battery voltage
{ PM100 temperature

14

{ Max cell temperature

The following warnings must be displayed on the LCD screen { Main battery voltage low

{ PM100 temperature high { Max cell temperature high

The following errors must be displayed on the LCD screen { Battery voltage below limit

{ PM100 temperature above limit { Max cell temperature above high { BMS error

{ Insulation Monitoring Device { PM100 Error

6.2.3 Performance Testing

Project Requirements: "The unit must boot up in less than 30 seconds."

6.2.4 Load testing

Verify the system response when CAN network is heavily loaded.

6.2.5 Stress Testing

None.

6.2.6 Ruggedized Testing

Requirements Document: "The unit must be weatherproof." Ruggedized to survive one season of racing.

15

6.3 Test Strategy

The test strategy is the recommended approach to test the hardware and software. The previous section described what will be tested. This section describes how it will be tested.

6.3.1 Function Testing

The goal of these tests is to verify proper data acceptance, processing and transmission. This testing is based on black and white box techniques. These tests are to check that modules can handle typical situations.

Test Objective: | Ensure proper data entry, processing and transmission.
Technique: | Execute each use case, case ow, or function, data, to
| verify the expected results occur when valid data is used.
Completion Criteria: | All planned tests have been executed. All identi ed de-
| fects have been addressed.
Special Considerations: | N/A
| Table 3: Function Testing

6.3.2 User Interface Testing

The goal of these tests is to verify proper data acceptance, processing and transmission. This testing is based on black and white box techniques. These tests are to check that modules can handle typical situations.

16

Test Objective: | | Verify the following: Ensure the LCD screen displays
| | information properly on the screen and is visible to the
| | driver. Verify that screen is readable in sunlight.
Technique: | | Prede ned messages are broadcast over the CAN bus
| | and the corresponding information should be displayed
| | onto the screen. Take the unit outside and see if screen
| | is readable.
Completion Criteria: | | All user interface modules functioning properly. All
| | identi ed defects have been addressed.
Special Considerations: | | If visibility of screen in sunlight is sub-par a new type of
| | screen will need to be sourced and all interface testing
| | will have to be repeated.
| Table 4: User Interface Testing

6.3.3 Performance Testing

Performance testing measures the transaction time and other time sensitive requirements. The goal of of performance testing is to tune the system to ensure that interaction with the system is not excessively slow and doesn't use excessive energy.

Test Objective: | | Validate system response time for designated transac-
| | tions.
Technique: | | Measure the time it takes to perform predetermined op-
| | erations to ensure they complete within a satisfactory
| | time range.
Completion Criteria: | | Completion of operation is found to be satisfactory
| | based on predetermined time range.
Special Considerations: | | N/A
| Table 5: Performance Testing

17

6.3.4 Stress Testing

This section is not applicable to test the Digital Dash prototype.

6.3.5 Load Testing

Load testing measures the ability of the system to function properly under di erent workloads. The goal of the load testing is to determine and ensure the system functions properly beyond the expected maximum workload.

Test Objective: | Validate system response time for designated operations.
Technique: | Saturate the CAN bus with data to determine if data
| can properly be captured and processed.
Completion Criteria: | Data still properly displayed on screen without system
| locking up or becoming unusable.
Special Considerations: | N/A
| Table 6: Load Testing

6.3.6 Ruggedness Testing

Ruggedness testing veri es the operation of the unit while meeting Formula SAE Rules requirements and sponsor design requirements.

Test Objective: | | Verify unit adheres to requirements of Formula SAE ar-
| | ticle 7 EV7.33. Ensure meets any additional ruggedness
| | requirements.
Technique: | | Physical tests to ensure that enclosure can function after
| | being exposed to water for 240 seconds.
Completion Criteria: | | System is still operational after all tests have been com-
| | pleted.
Special Considerations: | | Exposed to water means rain like conditions not immer-
| | sion.
| Table 7: Ruggedness Testing

18

6.4 Testing Equipment

Equipment needed to carry out testing:

Windows compatible PC

Viking Motorsports electric race car EVCU Programming Software

Spray hose

6.5 Resources

Role | Minimum | Resources | Speci c | responsibilities/
| Recommended | | Comments
Test Designer | Chad Thueson | | Identi es, prioritizes, and
| | | | implements test cases.
System Testers | Chad Thueson, | Sean | Executes tests, | log results,
| Koppenha er, | Jaime | recover from erros, docu-
| Rodriguez, | Noah Er- | ment defects
| ickson, Rishal Dass
Designer | Chad Thueson | | Identi es and de nes the
| | | | operations, | attributes, | and
| | | | associations | of | the | test
| | | | classes.
Implementer | Chad Thueson | | Implements and unit tests
| | | | the test classes and test
| | | | packages.

Table 8: Resources

6.6 Results

Test good.

19

7 Conclusion

The digital dashboard performs as intended when simulated with the demo program that we created. Instead of testing all functionally of the screen, the demo program focuses on only the most important functions.

Due to circumstances outside of our control, the digital dashboard has not been o cially tested on the electric vehicle but we are con dent that it would function correctly.

8 LICENSING INFORMATION

This work is licensed under a Creative Commons Attribution-ShareAlike 4.0 International License.

References

[Figueredo and Wolf, 2009] Figueredo, A. J. and Wolf, P. S. A. (2009). Assortative pairing and life history strategy - a cross-cultural study. Human Nature, 20:317{330.

20

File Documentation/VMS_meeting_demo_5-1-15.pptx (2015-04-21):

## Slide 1

Sean Koppenhafer, Jaime Rodriguez,
Chad Thueson, Noah Erickson, Rishal Dass

Digital Dash

Portland State University

Department of Electrical and Computer Engineering (ECE)


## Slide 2

Project Overview

- Electric systems add complexity and a traditional LED dash won't suffice
- Drivers must be aware of system faults and warnings
- An LCD Dashboard must be created to accommodate additional electrical systems

Formula SAE Electric Car


Current Traditional LED Dash


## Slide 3

Progress

- Completed

- Arduino can get RMS and BMS data
- Screen can output BMS and RMS data
- Prototype software and hardware works completely
- Lots of documentation

- Still to accomplish

- Assemble final board
- Program final board
- Assemble the demo unit
- Create enclosure

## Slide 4

Block Diagram


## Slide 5

Software


- Arduino Code

- Searches for specific CAN message ID’s, specified in code
- Sends messages via serial to the screen module (uses a visi-genie library)
- Currently running on an Arduino Due but will port over to the custom PCB

- 4D Visi-Genie

- Controls the positioning of the gauges, bars and symbols
- Handles button presses and their submenus
- Scales code sent from Arduino Due to match output data

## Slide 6

Screen Module

- 4D Systems uLCD-35DT
  - 3.5” Resistive Touch Screen
  - Display Module handles graphics processing and image storage
- User Interface
  - IMD, BMS and Motor symbols act as buttons to get into submenus
  - Battery level, Motor
temp and amperage
displayed


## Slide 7

Enclosure Designs

?

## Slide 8

Prototype Boards

- Power & Can Transceivers
  - The CAN transceivers receive data from the BMS and RMS and send them to the Arduino Due
  - Power Board steps 12V down to 5V also includes CAN transceiver circuitry
    - The TLF1963 Voltage runs very hot
    - May end up just using 5V from GeVCU
- Arduino Due
  - Runs the software for processing CAN messages and mapping them to the screen module


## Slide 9

Prototype Enclosure

- Simple enclosure for track day testing
  - Mounted to the driver side pod to eliminate blind spots
  - Track day enclosure is also water resistant
  - Arduino Due, power board and screen secured in box
  - This enclosure was quickly created for a track day prototype and is not intended for the final unit


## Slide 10

Custom PCB

- Why a custom PCB?
  - Cut down on total dash board size
  - Designed to plug directly into the back of the screen module
- Components
  - Contains the essentials of an Arduino Due and the prototype power board with CAN transceivers
- Other Details
  - Manufactured by OSH Park
  - 3 boards were manufactured

Include a side by side picture of
the Arduino Due size vs PCB

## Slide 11

Final Enclosure

- Requirements
  - Waterproof
- Dimensions
  - Must be low profile to fit in dash
  - Viewing angle is a bit awkward, through the steering wheel


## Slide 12

Demonstration Unit

- Unit Created to Simulate Car
  - Runs off the Arduino Due used for prototyping
  - Will be used to demonstrate project
- Hardware
  - Potentiometers and buttons to simulate functionality of the car
- Software
  - Sends input data from potentiometers and buttons to the digital dash unit

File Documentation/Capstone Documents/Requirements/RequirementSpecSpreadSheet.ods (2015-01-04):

REQUIREMENTS SPECIFICATION
Marketing Requirements | Engineering Requirements | Justification
2 | The unit must have a trans-reflective screen capable of 500-900 nits. | The digital dash will be used in direct sunlight and must be readable in such conditions.
5 | It must be able to be powered by a 12V DC source. | The unit will be powered from the main battery on board the electric car.
5 | A power supply must be designed for the digital dash to be robust against electrical noise. | The 12V battery is just a nominal value. The actual value will fluctuate quite a bit and the digital dash must operate at a fluctuating voltage.
5 | The electric car must run with or without the display. | In case of digital dash failure the electric car must still be operable.
3,5 | Unit must boot up in less than 30 seconds. | The digital dash must boot up quickly so it is not a nuisance to turn on and use.
3,5 | The digital dash should be reasonably simple to reconfigure and add/remove variable/messages to display | The digital dash must be easy for another user to add information to it with a user manual.
2 | The unit must be weather-proof. | The digital dash will be used in rain and must be usable in such conditions.
1 | Total parts and manufacturing should not exceed $500. | The digital dash must be relatively cheap to accommodate the Viking Motorsport budget.
3,4 | The digital dash should be easily readable, big fonts, non cluttered display | The operator will need to quickly glance at the display and get information quickly.
4,5 | The digital dash should be small and easily mounted | The electric car dash does not have a lot of space available and will need to be moved around easily.
3,5 | The digital dash should gather data from the VCU to display to the dash. | The electric car is already logging all the information that needs to be displayed on the digital dash.
1. The system should have a cost of $500 or less.
2. The display should be usable in all weather conditions.
3. The system should alert the operator to system warnings.
4. The system should be physically small.
5. The system should be easy to install.

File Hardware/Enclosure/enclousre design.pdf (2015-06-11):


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
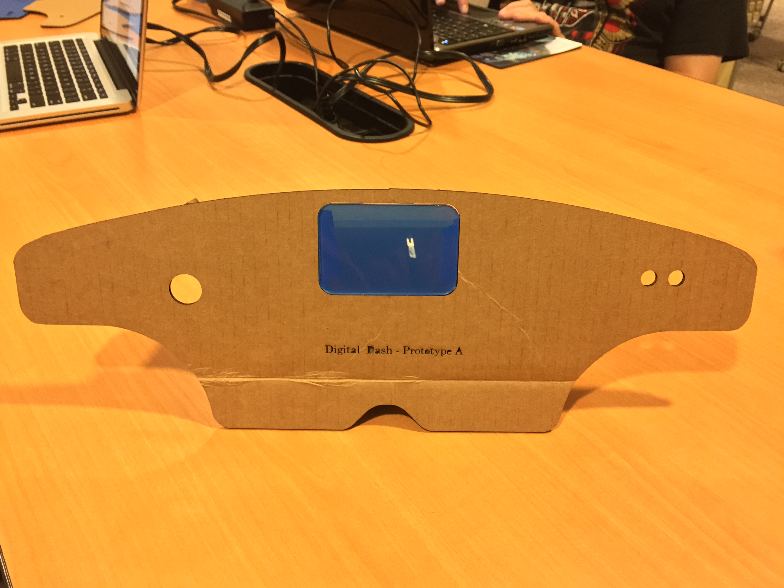
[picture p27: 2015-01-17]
images/Pictures/Design Prototype.JPG

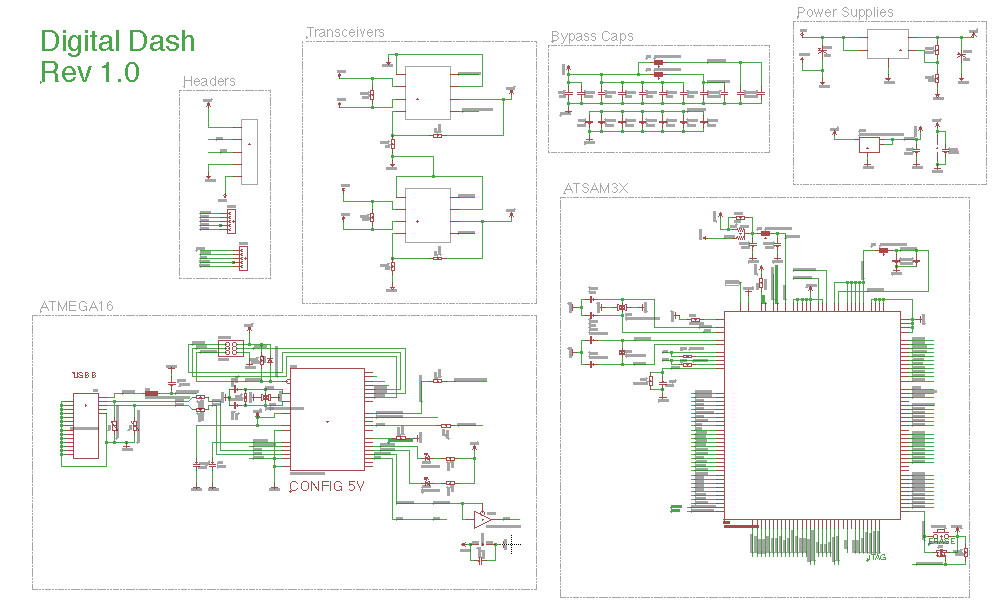
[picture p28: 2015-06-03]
images/Diagrams/schematic.jpg

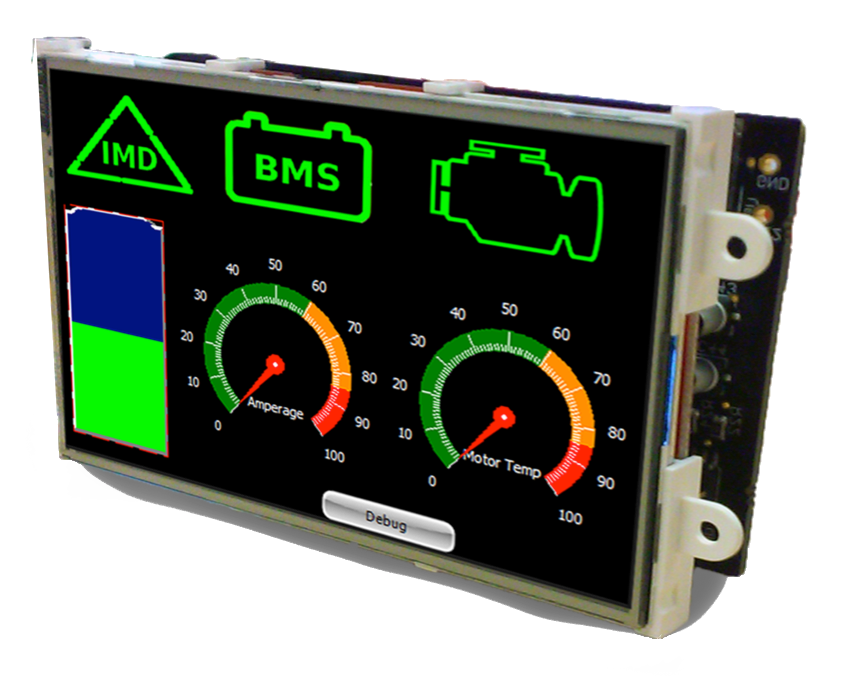
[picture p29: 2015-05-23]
images/Poster/screen.tiff

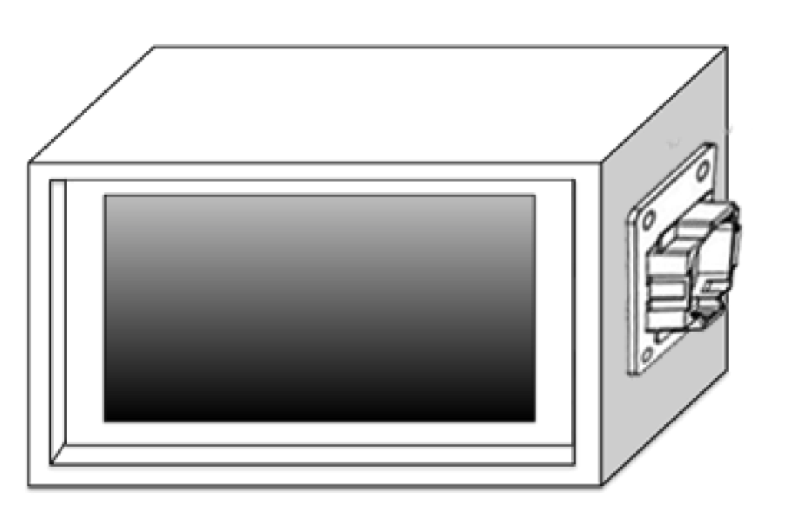
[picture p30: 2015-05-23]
images/Poster/final unit.png

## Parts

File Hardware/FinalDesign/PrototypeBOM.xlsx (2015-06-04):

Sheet: Ver.2
 | Ordered | Comments | Part Ref | Item | Eagle Number | DigiKey Part Number | Quantity | Unit Price | Extended Price | Link
Capacitors | X | C23,24-NM | C(21:25),39,40 | 22pF Capacitor | C-EUC0805 | 399-1113-1-ND | 5 | $0.10 | $0.50 | http://www.digikey.com/product-detail/en/C0805C220J5GACTU/399-1113-1-ND/411388
 | X |  | C38 | 1uF Capacitor | C-EUC0805 | 399-1284-1-ND | 1 | $0.12 | $0.12 | http://www.digikey.com/product-detail/en/C0805C105K4RACTU/399-1284-1-ND/416060
 | X |  | C(4:10),(12:19),28,30,32,34,36,37 | .1uF Capacitor | C-EUC0805 | 1276-1003-1-ND | 21 | $0.10 | $2.10 | http://www.digikey.com/product-detail/en/CL21B104KBCNNNC/1276-1003-1-ND/3889089
 | x |  | C(1:3),11,29,33 | 10uF Cap, tantalum | CPOL-EUSMCB | 511-1447-1-ND | 6 | $0.58 | $3.48 | http://www.digikey.com/product-detail/en/TCP0J106M8R/511-1447-1-ND/923745
 | X |  | C43,44 | 10uF alum cap | CPOL-US153CLV-0405 | PCE4549CT-ND | 2 | $0.68 | $1.36 | http://www.digikey.com/product-detail/en/EEE-FPV100UAR/PCE4549CT-ND/1701048
Resistors
 | X | R8-NM | JR1,R8 | 0 Resistor | R-EU_R0805 | RHM0.0ARCT-ND | 1 | $0.10 | $0.10 | http://www.digikey.com/product-detail/en/MCR10EZPJ000/RHM0.0ARCT-ND/1214418
 | X |  | R19,20 | 22 Resistor | R-EU_R0805 | RHM22.0CRCT-ND | 2 | $0.10 | $0.20 | http://www.digikey.com/product-detail/en/MCR10EZPF22R0/RHM22.0CRCT-ND/1214182
 | X |  | R5,6 | 39 Resistor | R-EU_R0805 | RHM39CPCT-ND | 2 | $0.10 | $0.20 | http://www.digikey.com/product-detail/en/MCR10ERTJ390/RHM39CPCT-ND/4085192
 | X |  | R22,24,26,27 | 50 Resistor | R-EU_R0805 | RHM49.9AECT-ND | 4 | $0.16 | $0.64 | http://www.digikey.com/product-detail/en/ESR10EZPF49R9/RHM49.9AECT-ND/1983860
 | X |  | R25,28 | 120 Resistor | R-EU_R0805 | RHM120KCT-ND | 2 | $0.10 | $0.20 | http://www.digikey.com/product-detail/en/ESR10EZPJ121/RHM120KCT-ND/1762959
 | X |  | R14,15,17,21,23 | 1k Resistor | R-EU_R0805 | RHM1.00KCHCT-ND | 5 | $0.10 | $0.50 | http://www.digikey.com/product-detail/en/MCR10ERTF1001/RHM1.00KCHCT-ND/2796512
 | X |  | R16 | 3.5k Resistor | R-EU_R0805 | RHM3.48KBLDKR-ND | 1 | $0.29 | $0.29 | http://www.digikey.com/product-detail/en/TRR10EZPF3481/RHM3.48KBLDKR-ND/2293399
 | X |  | R7 | 6.8k Resistor | R-EU_R0805 | 1276-5320-1-ND | 1 | $0.10 | $0.10 | http://www.digikey.com/product-detail/en/RC2012F682CS/1276-5320-1-ND/3968292
 | X |  | R13,18,99 | 10k Resistor | R-EU_R0805 | RHM10.0KCHCT-ND | 3 | $0.10 | $0.30 | http://www.digikey.com/product-detail/en/MCR10ERTF1002/RHM10.0KCHCT-ND/2796513
 | X |  | R4 | 100k Resistor | R-EU_R0805 | RHM100KCHCT-ND | 1 | $0.10 | $0.10 | http://www.digikey.com/product-detail/en/MCR10ERTF1003/RHM100KCHCT-ND/2796514
 | X | R9-NM | R9 | 1M_NM Resistor | R-EU_R0805 | RHM1.00MAHCT-ND | 1 | $0.17 | $0.17 | http://www.digikey.com/product-detail/en/KTR10EZPF1004/RHM1.00MAHCT-ND/1983952
 | x |  | Z3,4 | Variable Resistor | VARISTORCN0603 | CG0603MLC-05ECT-ND | 2 | $0.19 | $0.38 | http://www.digikey.com/product-detail/en/CG0603MLC-05E/CG0603MLC-05ECT-ND/3438061
Inductors
 | X |  | L1,2,3,5 | Ferrite Bead | WE-CBF_0805 | MH2029-300YCT-ND | 4 | $0.10 | $0.40 | http://www.digikey.com/product-detail/en/MH2029-300Y/MH2029-300YCT-ND/3741761
 | X |  | F2 | Resetable Fuse | MF-MSMF050-2 500mA | MF-MSMF050-2CT-ND | 1 | $0.22 | $0.22 | http://www.digikey.com/product-detail/en/MF-MSMF050-2/MF-MSMF050-2CT-ND/662842
IC#
 | X |  | IC1 | Opamp | LMV358IDGKR | 296-13455-1-ND | 1 | $0.82 | $0.82 | http://www.digikey.com/scripts/DkSearch/dksus.dll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
 | X |  | IC4 | 3.3V Regulator | MC33269ST-3.3T3 | MC33269ST-3.3T3GOSCT-ND | 1 | $0.97 | $0.97 | http://www.digikey.com/product-detail/en/MC33269ST-3.3T3G/MC33269ST-3.3T3GOSCT-ND/2120818
 | X |  | IC6 | ATMega16U2 | ATMEGA16U2-MU | ATMEGA16U2-MU-ND | 1 | $4.35 | $4.35 | http://www.digikey.com/product-detail/en/ATMEGA16U2-MU/ATMEGA16U2-MU-ND/2050821
 | X |  | IC10 | 5.5V Buffer | 74LVC1G125DCK | 296-11604-1-ND | 1 | $0.40 | $0.40 | http://www.digikey.com/product-detail/en/SN74LVC1G125DCKR/296-11604-1-ND/385743
 | X |  | ICSP | 2x3 Pin Header | PINHD-2X3 | 609-4517-ND | 1 | $0.70 | $0.70 | http://www.digikey.com/product-detail/en/67996-420HLF/609-3221-ND/1878553
MISC
 | X |  | T3 | MOSFETs | PMOSSOT23 | FDN340PCT-ND | 1 | $0.44 | $0.44 | http://www.digikey.com/product-detail/en/FDN340P/FDN340PCT-ND/965604
 | X | Check DIM | J3 | USB Micro | MYCON2_USB-MINI-B | WM1399CT-ND | 1 | $0.87 | $0.87 | http://www.digikey.com/product-detail/en/1050170001/WM1399CT-ND/2350885
U#
 | X |  | U1 | ATSAM3X | ATSAM3X/AAU | ATSAM3X8EA-AU-ND | 1 | $12.60 | $12.60 | http://www.digikey.com/product-detail/en/ATSAM3X8EA-AU/ATSAM3X8EA-AU-ND/3128687
 | X |  | U5 | Voltage Regulator | TLF1963TBATMA1CT-ND | TLF1963TBATMA1CT-ND | 1 | $2.89 | $2.89 | http://www.digikey.com/product-detail/en/TLF1963TBATMA1/TLF1963TBATMA1CT-ND/5052570
 | X |  | U2,4 | CAN Transceiver | MCP2551 | MCP2551T-I/SNTR-ND | 2 | $0.78 | $1.56 | http://www.digikey.com/product-detail/en/MCP2551T-I%2FSN/MCP2551T-I%2FSNTR-ND/509535
 | X |  | U3 | Display Connector | LCD_DISPLAY | S9275-ND | 1 | $3.04 | $3.04 | http://www.digikey.com/product-detail/en/PPPC052LFBN-RC/S7108-ND/810245
DIODES
 | X |  | D2 | Diode | DIODE-MINIMELF | CD1206-S01575CT-ND | 1 | $0.15 | $0.15 | http://www.digikey.com/product-detail/en/CD1206-S01575/CD1206-S01575CT-ND/3741949
 | X |  | RX1,TX1 | Yellow LED's | LEDCHIP-LED0805 | 160-1175-1-ND | 2 | $0.36 | $0.72 | http://www.digikey.com/product-detail/en/LTST-C170YKT/160-1175-1-ND/269247
Clocks
 | X |  | Y1 | 12MHz crystal | CRYSTAL-3.2-2.5 | CTX839CT-ND | 1 | $1.69 | $1.69 | http://www.digikey.com/product-detail/en/ECS-120-20-33-CKM-TR/XC1810CT-ND/2781935
 | X |  | Y4 | 16 MHz Crystal | CRYSTAL-3.2-2.5 | XC1810CT-ND | 1 | $0.79 | $0.79 | http://www.digikey.com/product-detail/en/ECS-160-20-33-TR/XC1137TR-ND/813224
 | X |  | Y2 | 32k Crystal | RESONATOR_EPSON_FC_145 | 535-9541-1-ND | 1 | $2.34 | $2.34 | http://www.digikey.com/scripts/DkSearch/dksus.dll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
Hardware
 | X |  | Y1 | 12MHz crystal | CRYSTAL-3.2-2.5 | CTX839CT-ND | 1 | $1.69 | $1.69 | http://www.digikey.com/product-detail/en/ECS-120-20-33-CKM-TR/XC1810CT-ND/2781935
 |  |  |  | 3/8 in pan head phillips | Sheet metal screws | 16 pack | 1 | $1.00
 |  | Need to Find |  | Button | MYSMD_PB157 |  | 1 |  | $0.00
 |  | DNP Stuff |  | NM 0 Resistor | R-EU_R0805 | RHM0.0ARCT-ND | 1 | $0.10 | $0.10 | http://www.digikey.com/product-detail/en/MCR10EZPJ000/RHM0.0ARCT-ND/1214418
 |  |  |  | 1M_NM Resistor | R-EU_R0805 | RHM1.00MAHCT-ND | 1 | $0.17 | $0.17 | http://www.digikey.com/product-detail/en/KTR10EZPF1004/RHM1.00MAHCT-ND/1983952
 |  |  |  | DNP -Pin Header | FE05-1 |  | 2 |  | $0.00
 |  |  |  | 22pF_NM Capacitor | C-EUC0805 | 399-1113-1-ND | 2 | $0.10 | $0.20 | http://www.digikey.com/product-detail/en/C0805C220J5GACTU/399-1113-1-ND/411388
 |  |  |  |  |  |  |  |  | $47.85
 |  |  |  |  |  | Total |  | $39.76
 |  |  |  |  |  |  |  | 0R |  | JR1 : 0R : R0805 : SmartPrj
 |  |  |  |  |  |  |  | 100K |  | R4 : 100K : R0805 : SmartPrj
 |  |  |  |  |  |  |  | 39R |  | R5 : 39R 1% : R0805 : SmartPrj
 |  |  |  |  |  |  |  | 39R |  | R6 : 39R 1% : R0805 : SmartPrj
 |  |  |  |  |  |  |  | 6k8 |  | R7 : 6k8 1% : R0805 : SmartPrj
 |  |  |  |  |  |  |  | 0RNM |  | R8 : 0R_NM : R0805 : SmartPrj
 |  |  |  |  |  |  |  | 1MNM |  | R9 : 1M_NM : R0805 : SmartPrj
 |  |  |  |  |  |  |  | 10k |  | R13 : 10K : R0805 : SmartPrj
 |  |  |  |  |  |  |  | 1k |  | R14 : 1K : R0805 : SmartPrj
 |  |  |  |  |  |  |  | 1k |  | R15 : 1K : R0805 : SmartPrj
 |  |  |  |  |  |  |  | 3.5k |  | R16 : 3.5K : R0805 : SmartPrj
 |  |  |  |  |  |  |  | 1k |  | R17 : 1K : R0805 : SmartPrj
 |  |  |  |  |  |  |  | 10k |  | R18 : 10K : R0805 : SmartPrj
 |  |  |  |  |  |  |  | 22r |  | R19 : 22R : R0805 : SmartPrj
 |  |  |  |  |  |  |  | 22r |  | R20 : 22R : R0805 : SmartPrj
 |  |  |  |  |  |  |  | 1k |  | R21 : 1K : R0805 : SmartPrj
 |  |  |  |  |  |  |  | 50 |  | R22 : 50 : R0805 : SmartPrj
 |  |  |  |  |  |  |  | 1k |  | R23 : 1K : R0805 : SmartPrj
 |  |  |  |  |  |  |  | 50 |  | R24 : 50 : R0805 : SmartPrj
 |  |  |  |  |  |  |  | 120 |  | R25 : 120 : R0805 : SmartPrj
 |  |  |  |  |  |  |  | 50 |  | R26 : 50 : R0805 : SmartPrj
 |  |  |  |  |  |  |  | 50 |  | R27 : 50 : R0805 : SmartPrj
 |  |  |  |  |  |  |  | 120 |  | R28 : 120 : R0805 : SmartPrj
 |  |  |  |  |  |  |  | 10k |  | R99 : 10K : R0805 : SmartPrj

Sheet: Sheet1
Unsure | Item | Eagle Number | DigiKey Part Number | Quantity | Unit Price | Extended Price | Link
 | 22pF Capacitor | C-EUC0805 | 399-1113-1-ND | 5 | $0.10 | $0.50 | http://www.digikey.com/product-detail/en/C0805C220J5GACTU/399-1113-1-ND/411388
 | 1uF Capacitor | C-EUC0805 | 399-1284-1-ND | 1 | $0.12 | $0.12 | http://www.digikey.com/product-detail/en/C0805C105K4RACTU/399-1284-1-ND/416060
 | .1uF Capacitor | C-EUC0805 | 1276-1003-1-ND | 21 | $0.10 | $2.10 | http://www.digikey.com/product-detail/en/CL21B104KBCNNNC/1276-1003-1-ND/3889089
 | Diode | DIODE-MINIMELF | CD1206-S01575CT-ND | 1 | $0.15 | $0.15 | http://www.digikey.com/product-detail/en/CD1206-S01575/CD1206-S01575CT-ND/3741949
 | Resetable Fuse | MF-MSMF050-2 500mA | MF-MSMF050-2CT-ND | 1 | $0.22 | $0.22 | http://www.digikey.com/product-detail/en/MF-MSMF050-2/MF-MSMF050-2CT-ND/662842
 | Opamp | LMV358MMX | LMV358MMX/NOPBCT-ND | 1 | $0.87 | $0.87 | http://www.digikey.com/product-detail/en/LMV358MMX%2FNOPB/LMV358MMX%2FNOPBCT-ND/3527087
 | 3.3V Regulator | MC33269ST-3.3T3 | MC33269ST-3.3T3GOSCT-ND | 1 | $0.97 | $0.97 | http://www.digikey.com/product-detail/en/MC33269ST-3.3T3G/MC33269ST-3.3T3GOSCT-ND/2120818
 | ATMega16U2 | ATMEGA16U2-MU | ATMEGA16U2-MU-ND | 1 | $4.35 | $4.35 | http://www.digikey.com/product-detail/en/ATMEGA16U2-MU/ATMEGA16U2-MU-ND/2050821
 | ATSAM3X | ATSAM3X/AAU | ATSAM3X8EA-AU-ND | 1 | $12.60 | $12.60 | http://www.digikey.com/product-detail/en/ATSAM3X8EA-AU/ATSAM3X8EA-AU-ND/3128687
 | 5.5V Buffer | 74LVC1G125DCK | 296-11604-1-ND | 1 | $0.40 | $0.40 | http://www.digikey.com/product-detail/en/SN74LVC1G125DCKR/296-11604-1-ND/385743
 | 2x3 Pin Header | PINHD-2X3 | 609-4517-ND | 1 | $0.70 | $0.70 | http://www.digikey.com/product-detail/en/77313-422R06LF/609-4517-ND/2665635
 | USB Micro | MYCON2_USB-MINI-B | WM1399CT-ND | 1 | $0.87 | $0.87 | http://www.digikey.com/product-detail/en/1050170001/WM1399CT-ND/2350885
 | 0 Resistor | R-EU_R0805 | RHM0.0ARCT-ND | 1 | $0.10 | $0.10 | http://www.digikey.com/product-detail/en/MCR10EZPJ000/RHM0.0ARCT-ND/1214418
 | 22 Resistor | R-EU_R0805 | RHM22.0CRCT-ND | 2 | $0.10 | $0.20 | http://www.digikey.com/product-detail/en/MCR10EZPF22R0/RHM22.0CRCT-ND/1214182
 | 39 Resistor | R-EU_R0805 | RHM39CPCT-ND | 2 | $0.10 | $0.20 | http://www.digikey.com/product-detail/en/MCR10ERTJ390/RHM39CPCT-ND/4085192
 | 50 Resistor | R-EU_R0805 | RHM49.9AECT-ND | 4 | $0.16 | $0.64 | http://www.digikey.com/product-detail/en/ESR10EZPF49R9/RHM49.9AECT-ND/1983860
 | 120 Resistor | R-EU_R0805 | RHM120KCT-ND | 2 | $0.10 | $0.20 | http://www.digikey.com/product-detail/en/ESR10EZPJ121/RHM120KCT-ND/1762959
 | 1k Resistor | R-EU_R0805 | RHM1.00KCHCT-ND | 5 | $0.10 | $0.50 | http://www.digikey.com/product-detail/en/MCR10ERTF1001/RHM1.00KCHCT-ND/2796512
 | 3.5k Resistor | R-EU_R0805 | RHM3.48KBLDKR-ND | 1 | $0.29 | $0.29 | http://www.digikey.com/product-detail/en/TRR10EZPF3481/RHM3.48KBLDKR-ND/2293399
 | 6.8k Resistor | R-EU_R0805 | 1276-5320-1-ND | 1 | $0.10 | $0.10 | http://www.digikey.com/product-detail/en/RC2012F682CS/1276-5320-1-ND/3968292
 | 10k Resistor | R-EU_R0805 | RHM10.0KCHCT-ND | 3 | $0.10 | $0.30 | http://www.digikey.com/product-detail/en/MCR10ERTF1002/RHM10.0KCHCT-ND/2796513
 | 100k Resistor | R-EU_R0805 | RHM100KCHCT-ND | 1 | $0.10 | $0.10 | http://www.digikey.com/product-detail/en/MCR10ERTF1003/RHM100KCHCT-ND/2796514
 | Ferrite Bead | WE-CBF_0805 | MH2029-300YCT-ND | 4 | $0.10 | $0.40 | http://www.digikey.com/product-detail/en/MH2029-300Y/MH2029-300YCT-ND/3741761
 | Yellow LED's | LEDCHIP-LED0805 | 160-1175-1-ND | 2 | $0.36 | $0.72 | http://www.digikey.com/product-detail/en/LTST-C170YKT/160-1175-1-ND/269247
 | MOSFETs | PMOSSOT23 | FDN340PCT-ND | 1 | $0.44 | $0.44 | http://www.digikey.com/product-detail/en/FDN340P/FDN340PCT-ND/965604
 | Voltage Regulator | TLF1963TBATMA1CT-ND | TLF1963TBATMA1CT-ND | 1 | $2.89 | $2.89 | http://www.digikey.com/product-detail/en/TLF1963TBATMA1/TLF1963TBATMA1CT-ND/5052570
 | CAN Transceiver | MCP2551 | MCP2551T-I/SNTR-ND | 2 | $0.78 | $1.56 | http://www.digikey.com/product-detail/en/MCP2551T-I%2FSN/MCP2551T-I%2FSNTR-ND/509535
 | Pin Header | LCD_DISPLAY | S9275-ND | 1 | $3.04 | $3.04 | http://www.digikey.com/product-detail/en/SFM210-LPSE-D05-ST-BK/S9275-ND/2039579
 | 12MHz crystal | CRYSTAL-3.2-2.5 | CTX839CT-ND | 1 | $1.69 | $1.69 | http://www.digikey.com/product-detail/en/403C35D12M00000/CTX839CT-ND/2293004
 | 16 MHz Crystal | CRYSTAL-3.2-2.5 | XC1810CT-ND | 1 | $0.79 | $0.79 | http://www.digikey.com/product-detail/en/ECS-120-20-33-CKM-TR/XC1810CT-ND/2781935
 | 32k Crystal | RESONATOR_EPSON_FC_145 | 535-11455-1-ND | 1 | $2.34 | $2.34 | http://www.digikey.com/product-detail/en/ASH7K-32.768KHZ-T/535-11455-1-ND/2673405
 | Variable Resistor | VARISTORCN0603 | CG0603MLC-05ECT-ND | 2 | $0.19 | $0.38 | http://www.digikey.com/product-detail/en/CG0603MLC-05E/CG0603MLC-05ECT-ND/3438061
 | 10uF Cap, tantalum | CPOL-EUSMCB | 511-1447-1-ND | 6 | $0.58 | $3.48 | http://www.digikey.com/product-detail/en/TCP0J106M8R/511-1447-1-ND/923745
 | 10uF alum cap | CPOL-US153CLV-0405 | PCE4549CT-ND | 2 | $0.68 | $1.36 | http://www.digikey.com/product-detail/en/EEE-FPV100UAR/PCE4549CT-ND/1701048
Need to Find | Button | MYSMD_PB157 |  | 1 |  | $0.00
DNP Stuff | NM 0 Resistor | R-EU_R0805 | RHM0.0ARCT-ND | 1 | $0.10 | $0.10 | http://www.digikey.com/product-detail/en/MCR10EZPJ000/RHM0.0ARCT-ND/1214418
 | 1M_NM Resistor | R-EU_R0805 | RHM1.00MAHCT-ND | 1 | $0.17 | $0.17 | http://www.digikey.com/product-detail/en/KTR10EZPF1004/RHM1.00MAHCT-ND/1983952
 | DNP -Pin Header | FE05-1 |  | 2 |  | $0.00
 | 22pF_NM Capacitor | C-EUC0805 | 399-1113-1-ND | 2 | $0.10 | $0.20 | http://www.digikey.com/product-detail/en/C0805C220J5GACTU/399-1113-1-ND/411388
 |  |  |  |  |  | $46.04
 |  |  | Total |  | $36.95
 |  |  |  |  | 0R |  | JR1 : 0R : R0805 : SmartPrj
 |  |  |  |  | 100K |  | R4 : 100K : R0805 : SmartPrj
 |  |  |  |  | 39R |  | R5 : 39R 1% : R0805 : SmartPrj
 |  |  |  |  | 39R |  | R6 : 39R 1% : R0805 : SmartPrj
 |  |  |  |  | 6k8 |  | R7 : 6k8 1% : R0805 : SmartPrj
 |  |  |  |  | 0RNM |  | R8 : 0R_NM : R0805 : SmartPrj
 |  |  |  |  | 1MNM |  | R9 : 1M_NM : R0805 : SmartPrj
 |  |  |  |  | 10k |  | R13 : 10K : R0805 : SmartPrj
 |  |  |  |  | 1k |  | R14 : 1K : R0805 : SmartPrj
 |  |  |  |  | 1k |  | R15 : 1K : R0805 : SmartPrj
 |  |  |  |  | 3.5k |  | R16 : 3.5K : R0805 : SmartPrj
 |  |  |  |  | 1k |  | R17 : 1K : R0805 : SmartPrj
 |  |  |  |  | 10k |  | R18 : 10K : R0805 : SmartPrj
 |  |  |  |  | 22r |  | R19 : 22R : R0805 : SmartPrj
 |  |  |  |  | 22r |  | R20 : 22R : R0805 : SmartPrj
 |  |  |  |  | 1k |  | R21 : 1K : R0805 : SmartPrj
 |  |  |  |  | 50 |  | R22 : 50 : R0805 : SmartPrj
 |  |  |  |  | 1k |  | R23 : 1K : R0805 : SmartPrj
 |  |  |  |  | 50 |  | R24 : 50 : R0805 : SmartPrj
 |  |  |  |  | 120 |  | R25 : 120 : R0805 : SmartPrj
 |  |  |  |  | 50 |  | R26 : 50 : R0805 : SmartPrj
 |  |  |  |  | 50 |  | R27 : 50 : R0805 : SmartPrj
 |  |  |  |  | 120 |  | R28 : 120 : R0805 : SmartPrj
 |  |  |  |  | 10k |  | R99 : 10K : R0805 : SmartPrj

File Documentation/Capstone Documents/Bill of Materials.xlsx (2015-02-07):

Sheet: Sheet1
Protoype Board
Name of Component | Supplier Part Number | Manufacturer Part Number | Unit Price | Quantity | Shipping | Total | Link to Component
Arduino Due | A000062 | - | $47.50 | 1 | $8.99 | $56.49 | http://www.amazon.com/Arduino-A000062-Due/dp/B00A6C3JN2?pebp=1422406212053&peasin=B00A6C3JN2
MCP2551 transceivers | MCP2551-I/P-ND | MCP2551-I/P | $1.22 | 2 | $5.23 | $7.67 | http://www.digikey.com/product-search/en?KeyWords=MCP2551-I%2FP-ND%20&WT.z_header=search_go
uLCD-35DT-AR | 971-SK-35DT-AR | SK-35DT-AR | $94.16 | 1 | $7.99 | $103.15 | http://www.mouser.com/ProductDetail/4D-Systems/SK-35DT-AR/

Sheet: Sheet2
Custom Board
Name of Component | Supplier Part Number | Manufacturer Part Number | Unit Price | Quantity | Shipping | Total | Link to Component
Arduino Due | A000062 | - | $47.50 | 1 | $8.99 | $56.49 | http://www.amazon.com/Arduino-A000062-Due/dp/B00A6C3JN2?pebp=1422406212053&peasin=B00A6C3JN2
MCP2551 transceivers | MCP2551-I/P-ND | MCP2551-I/P | $1.22 | 2 | $5.23 | $7.67 | http://www.digikey.com/product-search/en?KeyWords=MCP2551-I%2FP-ND%20&WT.z_header=search_go
uLCD-35DT-AR | 971-SK-35DT-AR | SK-35DT-AR | $94.16 | 1 | $7.99 | $103.15 | http://www.mouser.com/ProductDetail/4D-Systems/SK-35DT-AR/

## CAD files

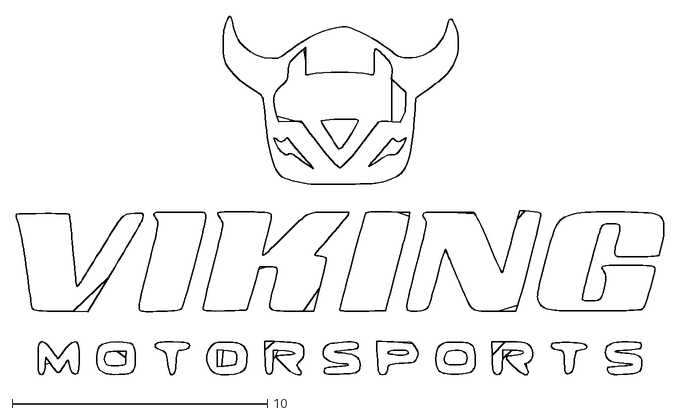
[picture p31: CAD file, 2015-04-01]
images/VMS_Logo/VMS LOGO.dxf
25.4 x 14.1

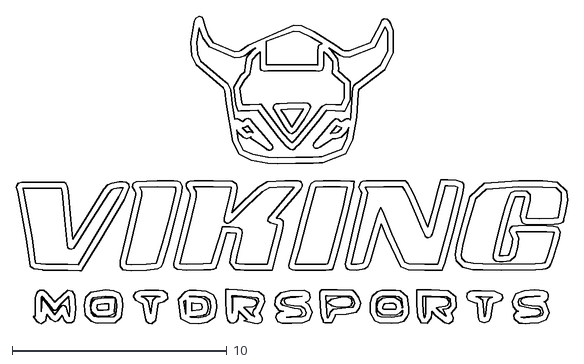
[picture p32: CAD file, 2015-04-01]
images/VMS_Logo/VMS LOGO1.dxf
25.7 x 14.3

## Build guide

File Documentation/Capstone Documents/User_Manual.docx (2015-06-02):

Viking Motorsports Digital Dashboard

Users Manual

Rev 1.1

May 2015

Getting Started

The Viking Motorsports Digital Dashboard System is comprised of a 4D Systems LCD screen and a custom circuit board based on the Arduino Due. The 4D Systems LCD screen is capable of resistive touch and the feature has been utilized in this package to provide for debugging capabilities. A driver should never need to touch the screen while driving.

Functionality of the digital dashboard has been kept simple to allow the driver and their crew to view information on the car with minimal hassle. Ease of use is a top priority with this project.

The Main Screen

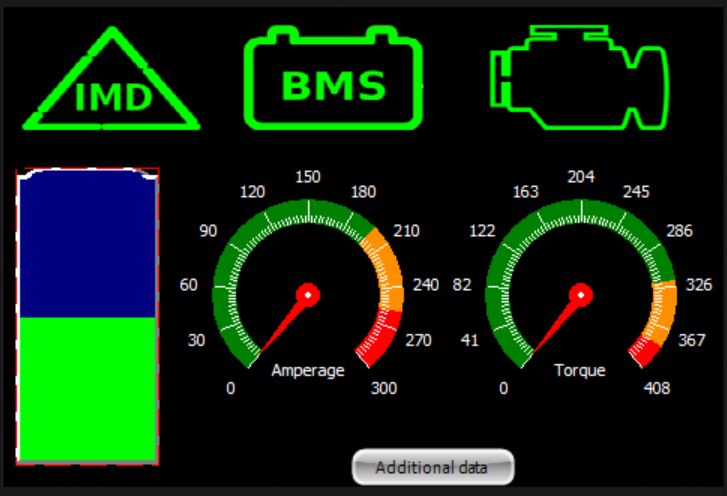
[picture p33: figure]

The main screen of the Digital Dashboard displays only the most important information for the driver while they are driving. Data displayed on the main screen includes motor torque, motor current, battery level, and IMD, BMS, and RMS system errors.

When an error occurs on the IMD, BMS or RMS sub-systems, their respective icon on the main screen will change from green to red. A green icon indicates there are no errors with the sub-system. A red icon indicates one or more errors with the sub-system.

The RMS and BMS icons are touch enabled. A user can touch either of the icons to be taken to a sub-screen that shows more in-depth information about the current errors on that sub-system. See the RMS/BMS Sub-Screen sections for more information.

Finally, there is a button at the bottom of the screen named additional data. Touching this button will take the user to a sub-screen that displays all data that the device receives on the addiontional information sub-screen. See the additional information sub-screen section for more information.

RMS Sub-Screen

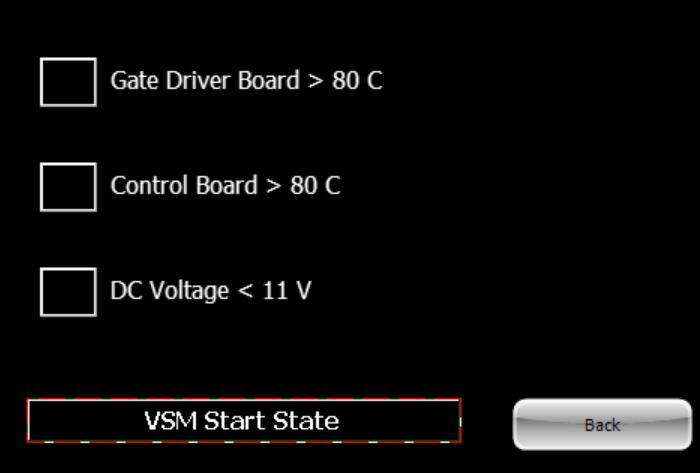
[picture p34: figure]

When an error occurs, the box next to the error will turn yellow. The RMS Sub-Screen contain warning LEDs for the following error conditions.

RMS Errors | Error Condition
Gate Driver Temperature | Greater than 80°C
Control Board Temperature | Greater than 80°C
12V Rail Voltage | Less than 11V for two seconds

On the bottom of the RMS sub-screen there is a button that the user can touch to return them to the main screen.

BMS Sub-Screen

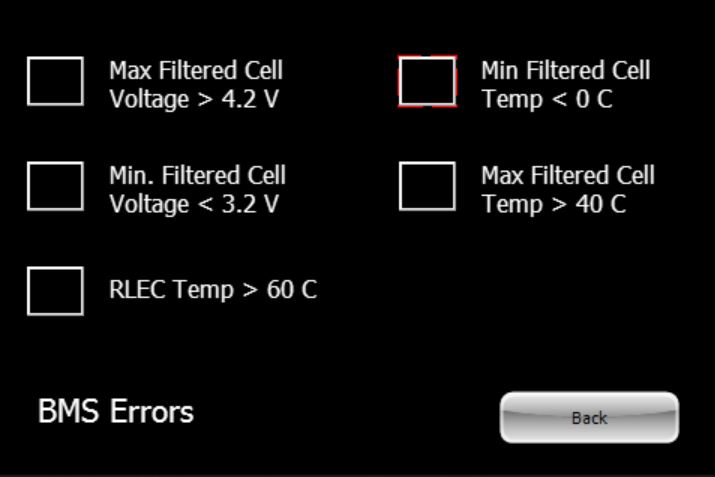
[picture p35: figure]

When an error occurs, the box next to the error will turn yellow. The BMS Sub-Screen contain warnings LEDs for the following error conditions.

BMS Errors | Error Condition
Maximum Battery Cell Voltage | Greater than 4.2V
Minimum Battery Cell Voltage | Less than 3.2V
RLEC Temperature | Greater than 60°C
Maximum Battery Cell Temperature | Greater than 40°C
Minimum Battery Cell Temperature | Less than 0°C

On the bottom of the BMS sub-screen there is a button that the user can touch to return them to the main screen.

Additional Information Sub-Screen

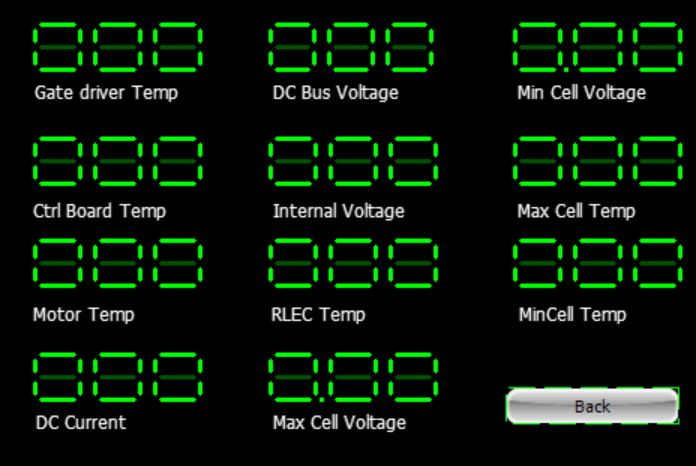
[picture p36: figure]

The additional information sub-screen displays all of the data that the dashboard collects from the car. This screen will have little to no use while driving the car. It has been included to assist in fixing issues with the car when a failure occurs.

On the bottom of the additional information sub-screen there is a button that the user can touch to return them to the main screen.

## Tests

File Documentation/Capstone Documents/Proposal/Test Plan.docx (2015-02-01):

Viking Motorsports Digital Dash

Test Plan

1/30/2015

V 1.2

Sean Koppenhoffer

Noah Erickson

Rishal Dass

Jaime Rodriquez

Chad Thueson

Objectives

  1.1. Purpose

This document describes the plan for testing the prototype of the Viking Motorsports Digital Dash. This Test Plan document supports the following objectives:

- Identify existing project information and the software and hardware that should be tested.
- List the recommended test requirements (high level).
- Recommend and describe the testing strategies to be employed
- Identify the required resources and provide an estimate of the test efforts.
- List the deliverable elements of all tests.
  1.2. Scope

This test plan describes the integration and system tests that will be conducted on the Viking motorsports digital dash following the integration of subsystems and components identified in the Design Considerations for prototyping document [1].

The purpose of this test plan is to test the feasibility and performance of the Digital Dash. It is critical that all subsystems be tested before integration into the system so as to ensure a proper user experience when using the digital dash is integrated into racing vehicle.

The following modules and interfaces will be tested:

- CAN message interpretation
- Data transmission to LCD
- GUI on LCD screen

Critical performance measures to test are:

- Minimal time to capture and interpret CAN data
- Time to display data on LCD screen after data interpretation
- Initialization time before the digital dash is ready to use
  1.3. References
1. Design Considerations, Version 1.0 (https://github.com/noahterickson/DigitalDash/wiki/Design-Considerations)
2. Digital Dash for an Electric Race Car (https://github.com/noahterickson/DigitalDash/blob/master/Requirements/Digital_Dash_Capstone.pdf)
1. Requirements for Test

The lists below identify items (functional requirements, non-functional requirements and use cases) that have been targeted for testing. This listing represents what will be tested.

  1.1. Function Testing
- Project requirements: The system must be powered by a 12V source
- Data from CAN network is being relayed to Arduino Due for analysis.
- Data from Arduino Due is being sent to LCD display.
- Data is being properly interpreted and displayed in GUI on LCD display.
  1.2. User Interface Testing
- LCD screen must be viewable in sunlight.
- Project requirements: “The digital dash should be easily readable, big fonts, non-cluttered display.”
- The following variables must be displayed on the LCD screen
  - Main battery voltage
  - PMI100 temperature
  - Max Cell temperature
- The following Warnings must be displayed on the LCD screen
  - Main battery voltage low
  - PM100 temperature high
  - Max cell temperature high
- The following errors must be displayed on the LCD screen
  - Battery voltage below limit
  - PM100 temperature above limit
  - Max cell temperature above high
  - BMS error
  - Insulation Monitoring Device error
  - PM100 error
  1.3. Performance Testing
- Project requirements: “The unit must boot up in less than 30 seconds.”
  1.4. Load Testing
- Verify system response when CAN network heavily loaded
  1.5. Stress Testing

None.

  1.6. Ruggedized Testing
- Requirements Document: “The unit must be weatherproof.” [2]
- Ruggedized to survive one season of racing.
2. Test Strategy

The test strategy is the recommended approach to test the hardware and software. The previous section described what will be tested. This section describes how it will be tested.

  2.1. Testing Types
    2.1.1. Function Testing

The goal of these tests is to verify proper data acceptance, processing and transmission. This testing is based on black and white box techniques. These tests are to check that modules can handle typical situations.

Test Objective: | - Ensure proper data entry and processing and transmission.
Technique: | - Execute each use case, case flow, or function, data, to verify the expected results occur when valid data is used.
Completion Criteria: | - All planned tests have been executed. - All identified defects have been addressed.
Special Considerations: | - N/A

    2.1.2. User Interface Testing

User Interface testing verifies a user’s interaction with the software. The goal of this testing is to ensure the UI provides appropriate feedback.

Test Objective: | - Verify the following: Ensure LCD screen displays information properly on the screen and is visible to the driver. - Verify that screen is readable in sunlight
Technique: | - Predefined messages are broadcast over the CAN network and the corresponding information should be displayed onto the screen - Take unit outside and see if screen is readable
Completion Criteria: | - All user interface modules functioning properly - All identified defects have been addressed
Special Considerations: | - If visibility of screen in sunlight is sub-par a new type of screen will need to be sourced and all interface testing will have to be repeated.

    2.1.3. Performance Testing

Performance testing measures the transaction time and other time sensitive requirements. The goal of performance testing is to tune the system to ensure that interaction with the system is not excessively slow and doesn’t use excessive energy.

Test Objective: | - Validate System Response time for designated transactions.
Technique: | - Measure the time it takes to perform predetermined operations to ensure they complete within a satisfactory time range.
Completion Criteria: | - Completion of operation is found to be satisfactory based on predetermined time range
Special Considerations: | - N/A

    2.1.4. Stress Testing

This section is not applicable to test the Digital Dash prototype.

    2.1.5. Load Testing

Load testing measures the ability of the system to function properly under different workloads. The goal of the load testing is to determine and ensure the system functions properly beyond the expected maximum workload.

Test Objective: | - Validate System Response time for designated operations.
Technique: | - Saturate CAN network with data to determine if data can properly be captured and processed.
Completion Criteria: | - Data still properly displayed on screen without system locking up or becoming unusable.
Special Considerations: | - NA

    2.1.6. Ruggedness Testing

Ruggedness testing verifies the operation of the unit while meeting Formula SAE Rules requirements and sponsor design requirements.

Test Objective: | - Verify unit adheres to requirements of Formula SEA Article 7 EV7.3.3 - Ensure meets any additional ruggedness requirements
Technique: | - Physical tests to ensure that enclosure can function after being exposed to water for 240 seconds
Completion Criteria: | - System is still operational after all tests have been completed.
Special Considerations: | - Exposed to water means rain like conditions not immersion

3. Testing Equipment

Equipment needed to carry out testing.

- Windows compatible PC
- Viking Motorsports electric race car
- EVCU programming software
- Spray hose
4. Resources

This section presents the recommended resources for testing the Digital Dash prototype.

5. Appendix Test Record Sheets
  5.1. Functional Test Cases

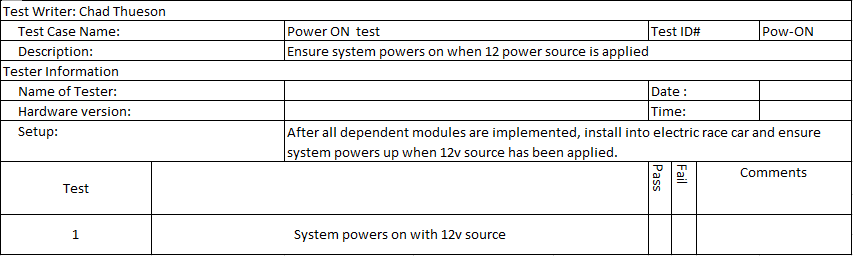
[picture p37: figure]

Test case for Power on

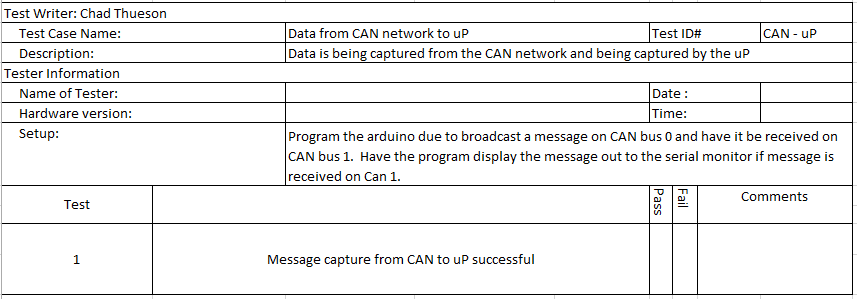
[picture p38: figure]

Test case for CAN to uP

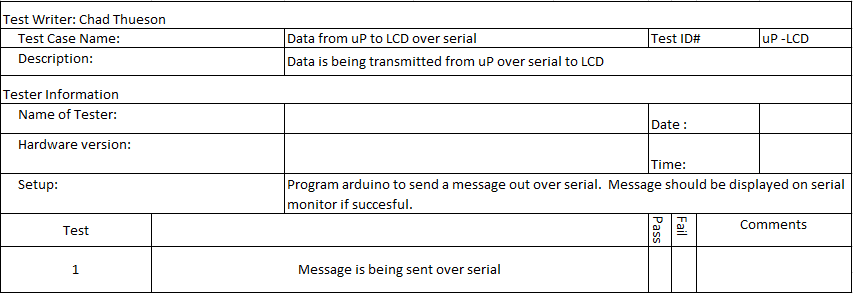
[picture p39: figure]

Test Case for uP to LCD

6.1 cont.

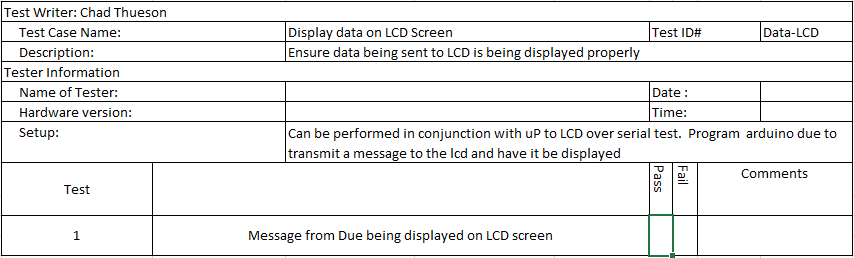
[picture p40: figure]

Test Case for displaying data on LCD screen

  5.2. User Interface Test Cases

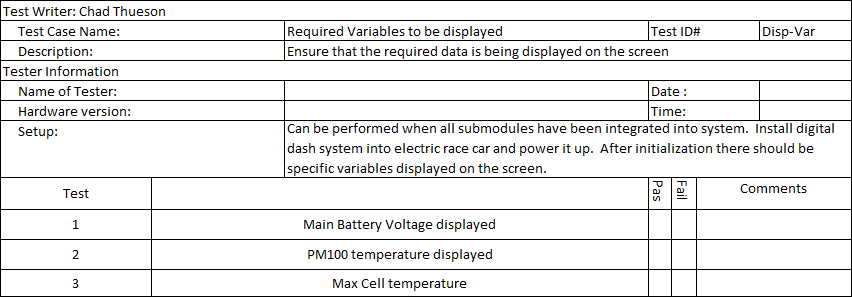
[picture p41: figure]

Test Case for required variable

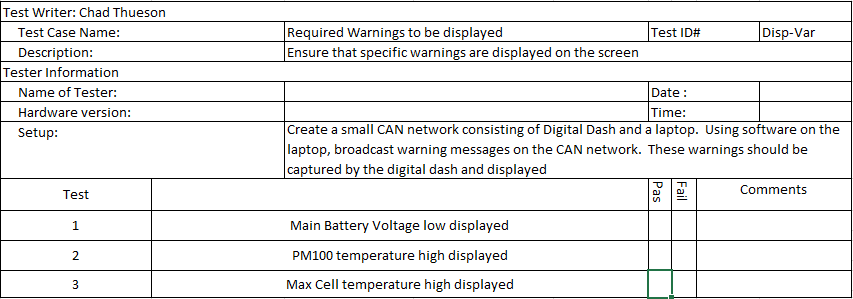
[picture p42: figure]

Test case for warnings displayed

6.2 cont.

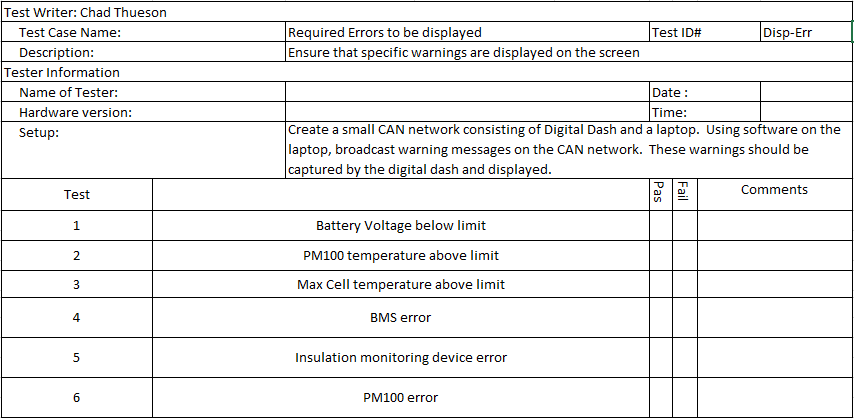
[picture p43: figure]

Test case error display

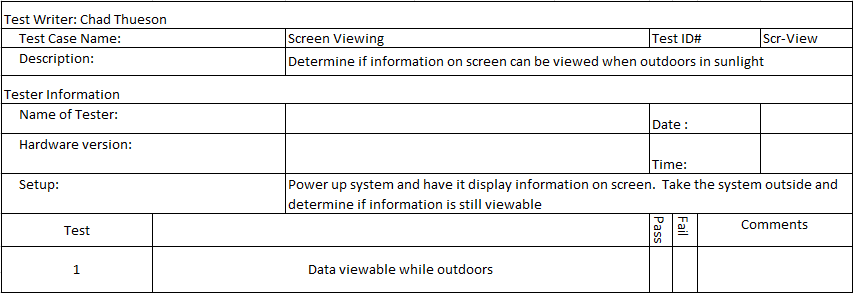
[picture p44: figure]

Test case for screen viewing in sunlight

  5.3. Performance Test Case

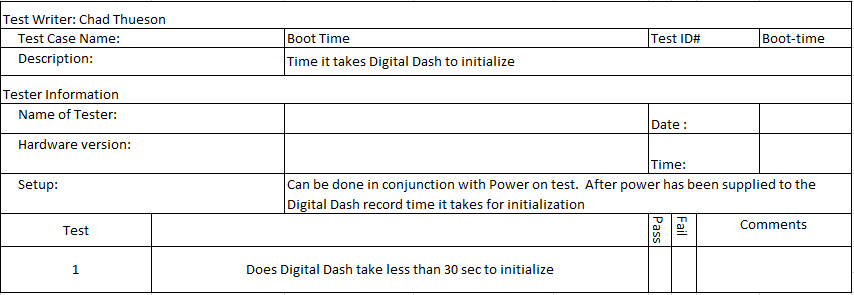
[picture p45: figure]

Test case for system boot time

  5.4. Load Test Case

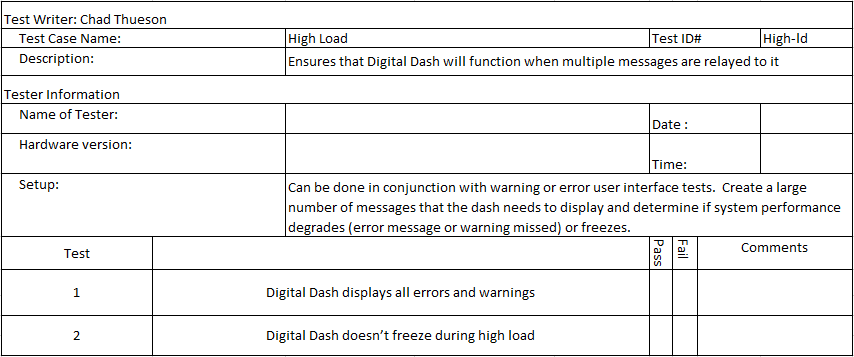
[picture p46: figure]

Test case high load

  5.5. Ruggedness Test Case


Test case for ruggedness/robustness

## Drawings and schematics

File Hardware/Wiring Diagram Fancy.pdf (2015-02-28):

# GE-‐vcu

## RMS

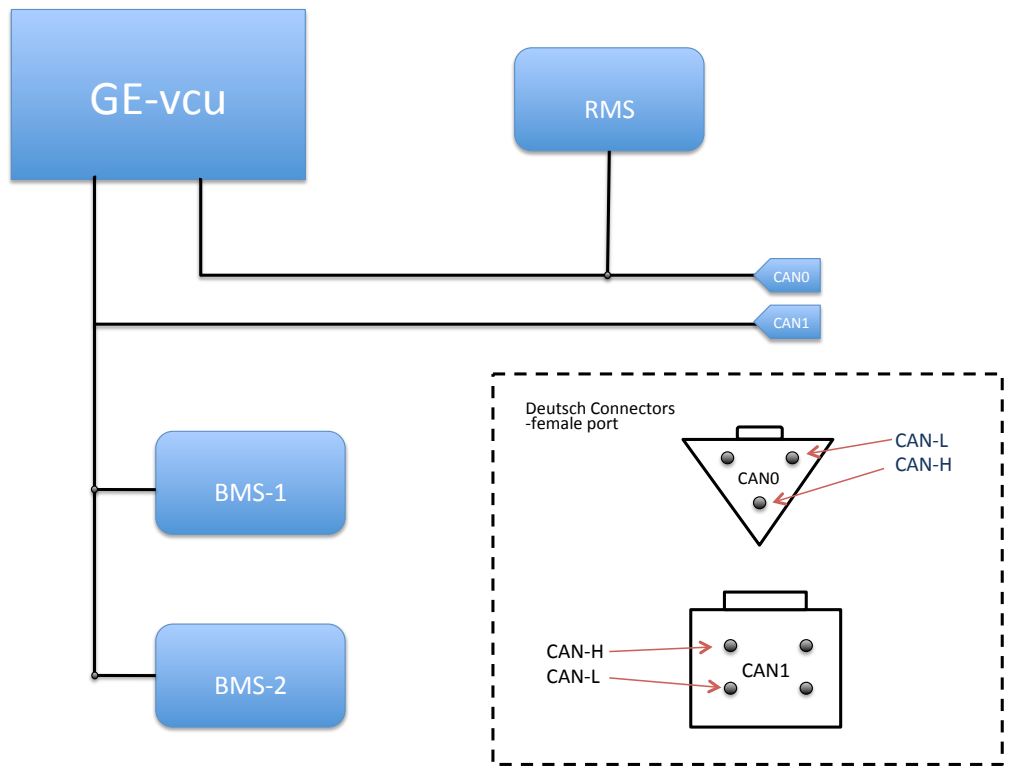
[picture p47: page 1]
BMS-‐1; BMS-‐2; CAN0; CAN1; CAN-‐L CAN-‐H; CAN-‐H CAN-‐L; Deutsch

Connectors -‐female port

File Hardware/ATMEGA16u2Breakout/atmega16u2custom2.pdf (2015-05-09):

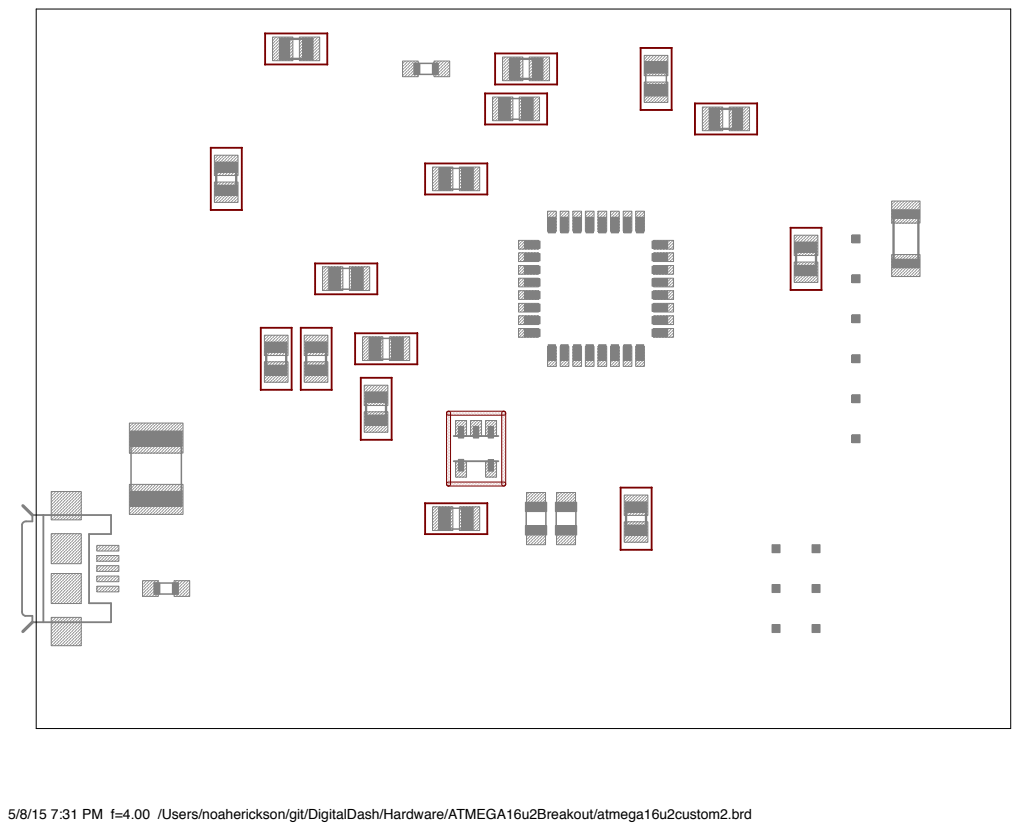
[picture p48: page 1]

5/8/15 7:31 PM f=4.00 /Users/noaherickson/git/DigitalDash/Hardware/ATMEGA16u2Breakout/atmega16u2custom2.brd

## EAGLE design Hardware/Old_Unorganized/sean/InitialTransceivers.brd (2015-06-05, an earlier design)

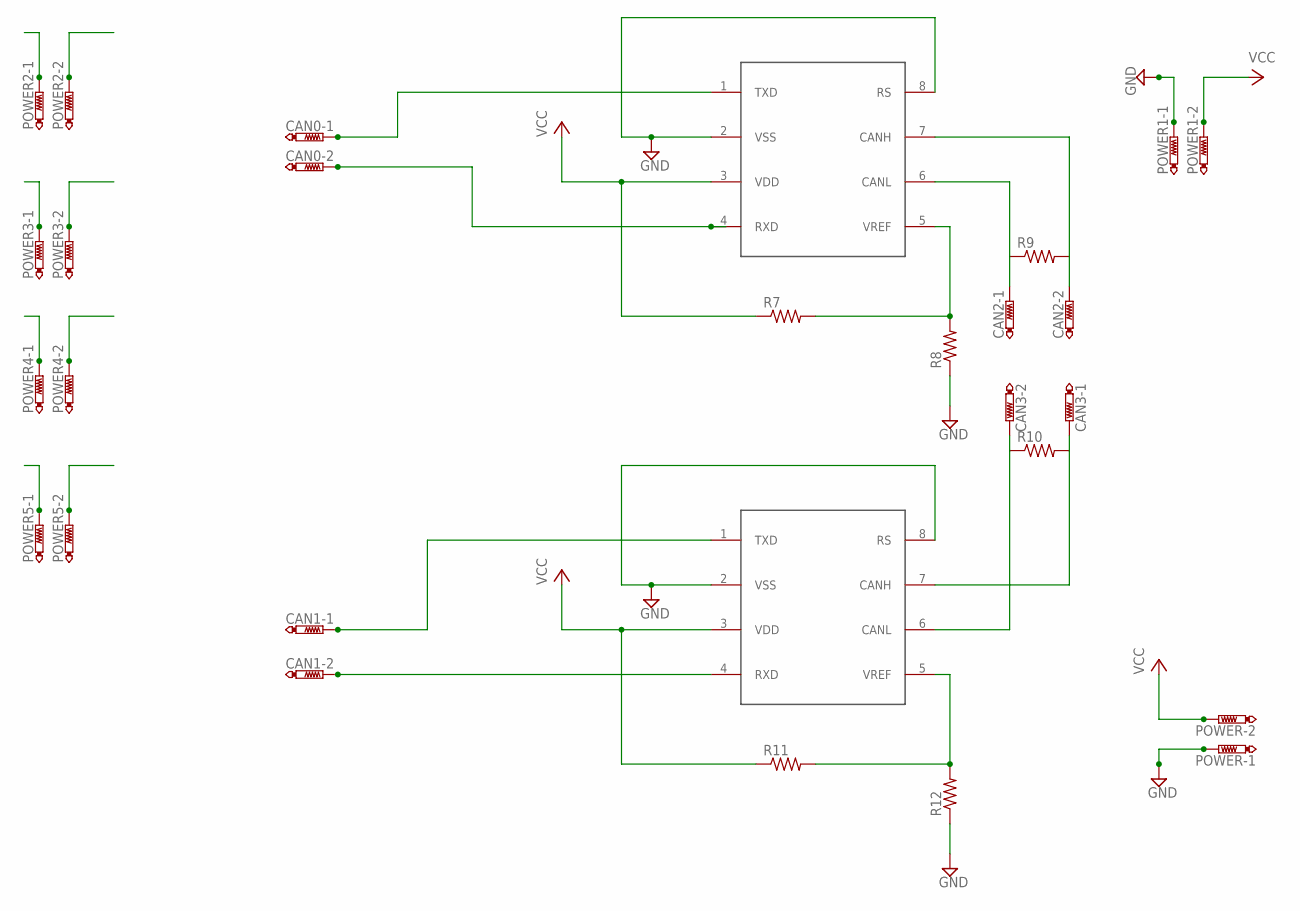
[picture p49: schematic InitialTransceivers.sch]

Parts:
CAN0, CAN1, CAN2, CAN3: PTR2; P2-38-17
POWER, POWER1, POWER2, POWER3, POWER4, POWER5: PTR2; P2-38-17
R7, R8, R9, R10, R11, R12: R-US_0204/5; 0204/5
U$2, U$3: MCP2551-DIP; DIL08

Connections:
A0: POWER2.TP-1, POWER3.TP-1
A1: POWER2.TP-2, POWER3.TP-2
A2: POWER4.TP-1, POWER5.TP-1
A3: POWER4.TP-2, POWER5.TP-2
CH: CAN3.TP-1, R10.2, U$3.7 (CANH)
CL: CAN3.TP-2, R10.1, U$3.6 (CANL)
GND: POWER.TP-1, POWER1.TP-1, R8.1, R12.1, U$2.2 (VSS), U$2.8 (RS), U$3.2 (VSS), U$3.8 (RS)
unnamed: CAN2.TP-1, R9.1, U$2.6 (CANL)
unnamed: CAN2.TP-2, R9.2, U$2.7 (CANH)
unnamed: R7.2, R8.2, U$2.5 (VREF)
unnamed: R11.2, R12.2, U$3.5 (VREF)
RX1: CAN0.TP-2, U$2.4 (RXD)
RX2: CAN1.TP-2, U$3.4 (RXD)
TX1: CAN0.TP-1, U$2.1 (TXD)
TX2: CAN1.TP-1, U$3.1 (TXD)
VCC: POWER.TP-2, POWER1.TP-2, R7.1, R11.1, U$2.3 (VDD), U$3.3 (VDD)

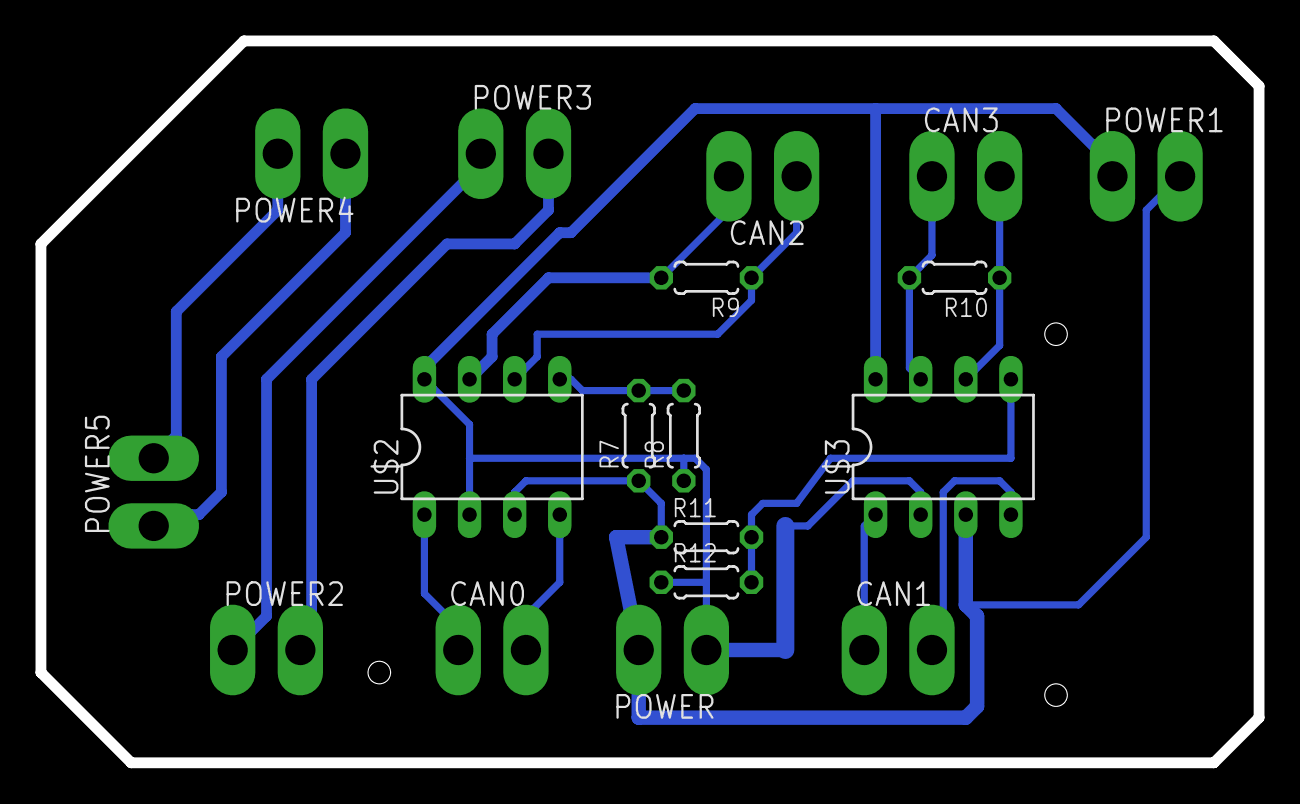
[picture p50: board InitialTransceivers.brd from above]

Board: 2 copper layers, 68.6 x 40.6 mm, 18 parts (0 on the bottom side), 16 nets.

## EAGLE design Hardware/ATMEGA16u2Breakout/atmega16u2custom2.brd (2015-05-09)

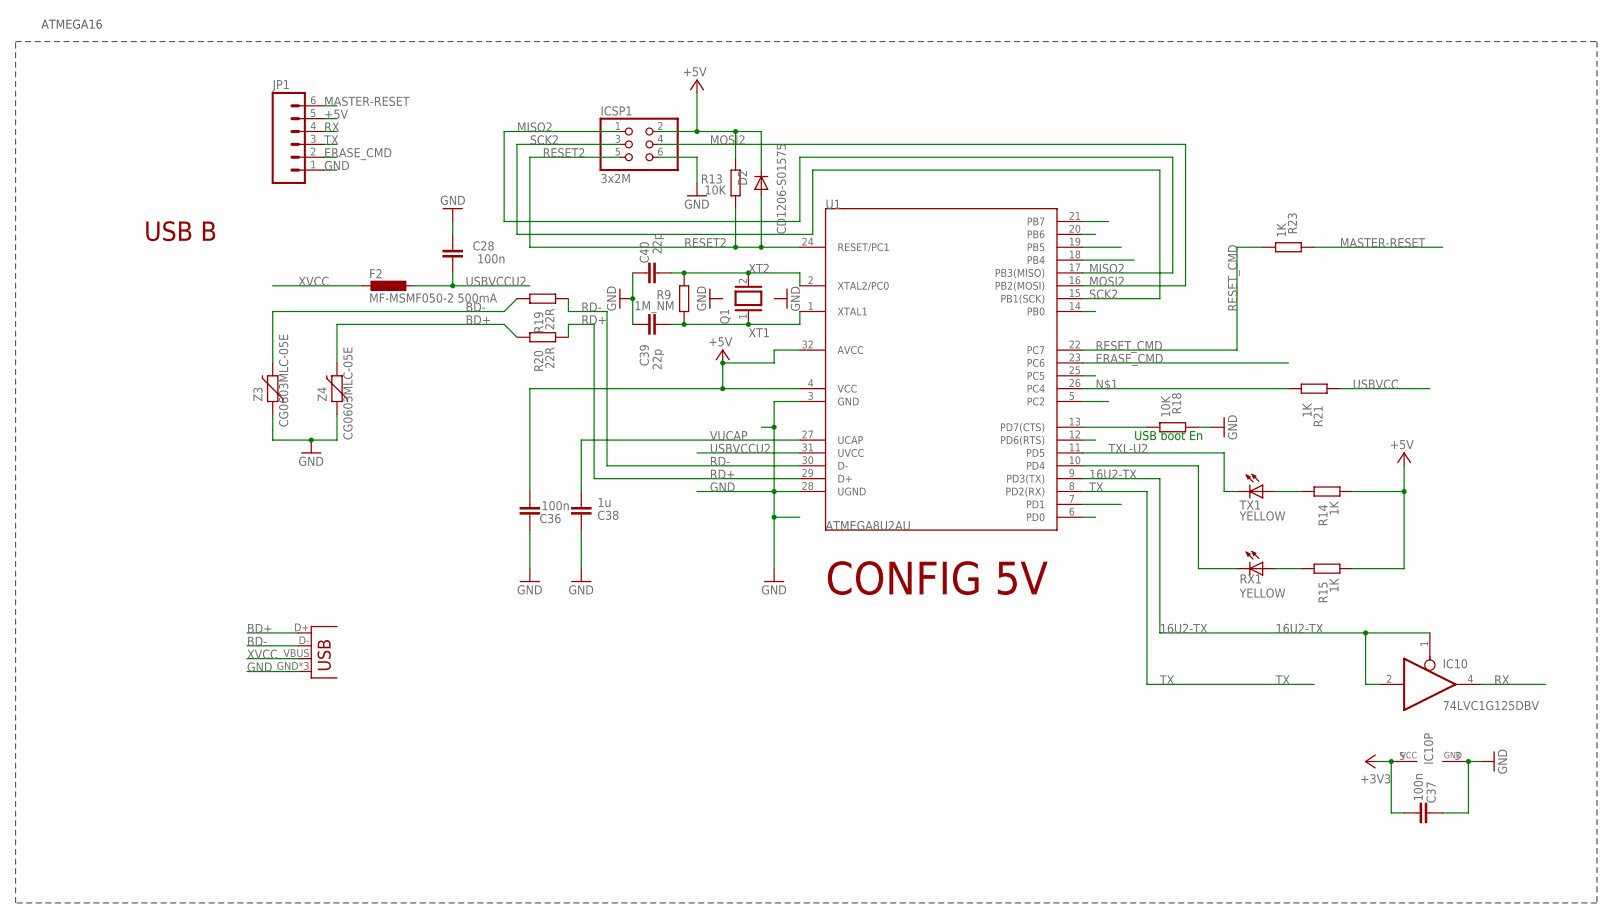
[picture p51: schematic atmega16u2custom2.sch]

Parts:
C28, C36, C37: 100n; C0805
C38: 1u; C0805
C39, C40: 22p; C0805
D2: CD1206-S01575; MINIMELF
F2: MF-MSMF050-2 500mA; L1812
IC10: 74LVC1G125DBV; SOT23-5
ICSP1: 3x2M; 2X03
JP1: M06NO_SILK; 1X06_NO_SILK
JP2: USB-MICROB
Q1: XTAL/S; QS
R9: 1M_NM; R0805
R13, R18: 10K; R0805
R14, R15, R21, R23: 1K; R0805
R19, R20: 22R; R0805
RX1: YELLOW; CHIP-LED0805
TX1: YELLOW; CHIP-LED0805
U1: ATMEGA8U2AU; TQFP32-08
Z3, Z4: CG0603MLC-05E; CT/CN0603

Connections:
8PB4: U1.18 (PB4)
8PB5: U1.19 (PB5)
8PB6: U1.20 (PB6)
16U2-TX: IC10.1 (OE), IC10.2 (I), U1.9 (PD3(TX))
+3V3: C37.1, IC10.5 (VCC)
+5V: C36.1, D2.C, ICSP1.2, JP1.5, R13.2, R14.1, R15.1, U1.4 (VCC), U1.32 (AVCC)
BD+: JP2.D+, R20.2, Z4.2
BD-: JP2.D-, R19.2, Z3.2
DTR: R18.1, U1.13 (PD7(CTS))
ERASE_CMD: JP1.2, U1.23 (PC6)
GND: C28.2, C36.2, C37.2, C38.2, C39.2, C40.2, IC10.3 (GND), ICSP1.6, JP1.1, JP2.GND, JP2.MT1 (GND), JP2.MT2 (GND), R18.2, U1.3 (GND), U1.28 (UGND), Z3.1, Z4.1
MASTER-RESET: JP1.6, R23.2
MISO2: ICSP1.1, U1.17 (PB3(MISO))
MOSI2: ICSP1.4, U1.16 (PB2(MOSI))
unnamed: R21.1, U1.26 (PC4)
unnamed: R15.2, RX1.A
unnamed: R14.2, TX1.A
RD+: R20.1, U1.29 (D+)
RD-: R19.1, U1.30 (D-)
RESET2: D2.A, ICSP1.5, R13.1, U1.24 (RESET/PC1)
RESET_CMD: R23.1, U1.22 (PC7)
RX: IC10.4 (O), JP1.4
RXL-U2: RX1.C, U1.10 (PD4)
SCK2: ICSP1.3, U1.15 (PB1(SCK))
TX: JP1.3, U1.8 (PD2(RX))
TXL-U2: TX1.C, U1.11 (PD5)
USBVCC: R21.2
USBVCCU2: C28.1, F2.1, U1.31 (UVCC)
VUCAP: C38.1, U1.27 (UCAP)
XT1: C39.1, Q1.1, R9.1, U1.1 (XTAL1)
XT2: C40.1, Q1.2, R9.2, U1.2 (XTAL2/PC0)
XVCC: F2.2, JP2.VBUS

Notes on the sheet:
USB boot En
CONFIG 5V
USB B
ATMEGA16

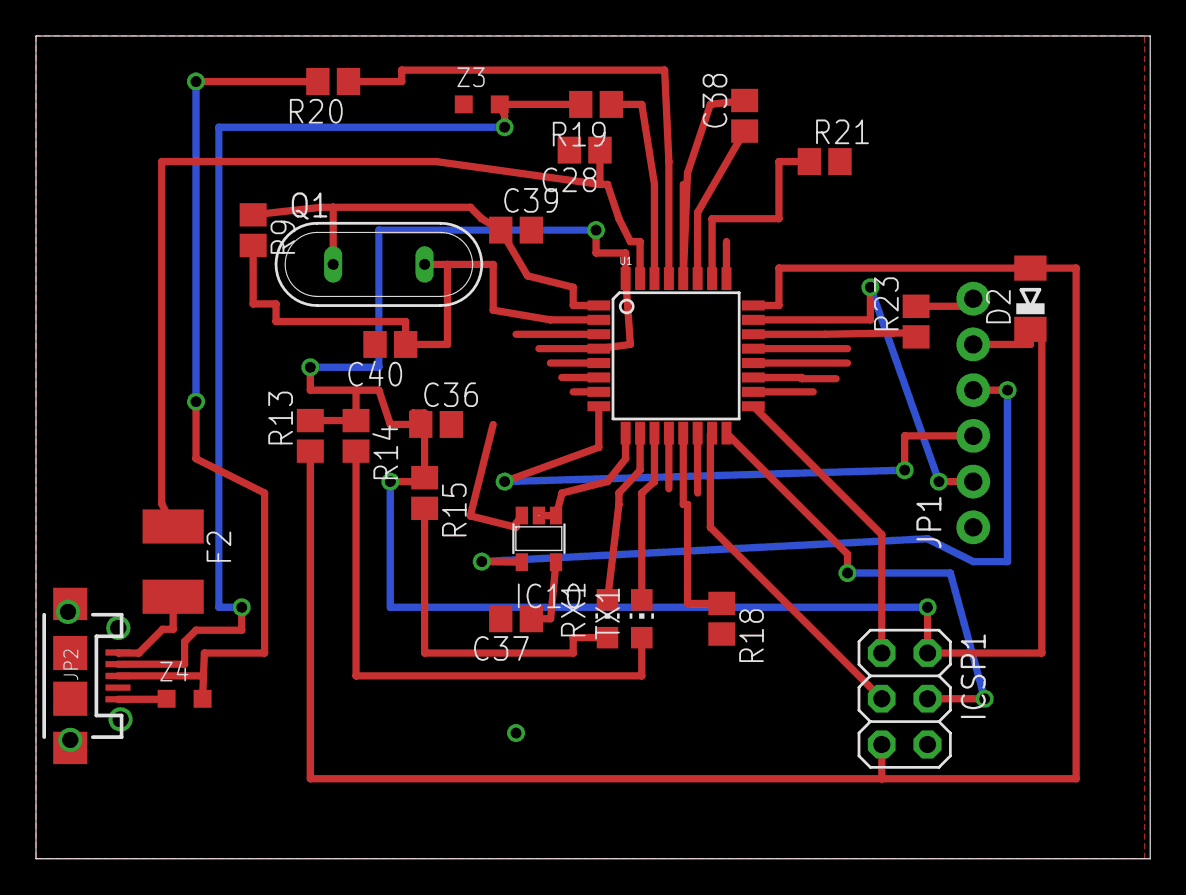
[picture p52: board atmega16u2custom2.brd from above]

Board: 2 copper layers, 61.9 x 45.7 mm, 27 parts (0 on the bottom side), 28 nets.

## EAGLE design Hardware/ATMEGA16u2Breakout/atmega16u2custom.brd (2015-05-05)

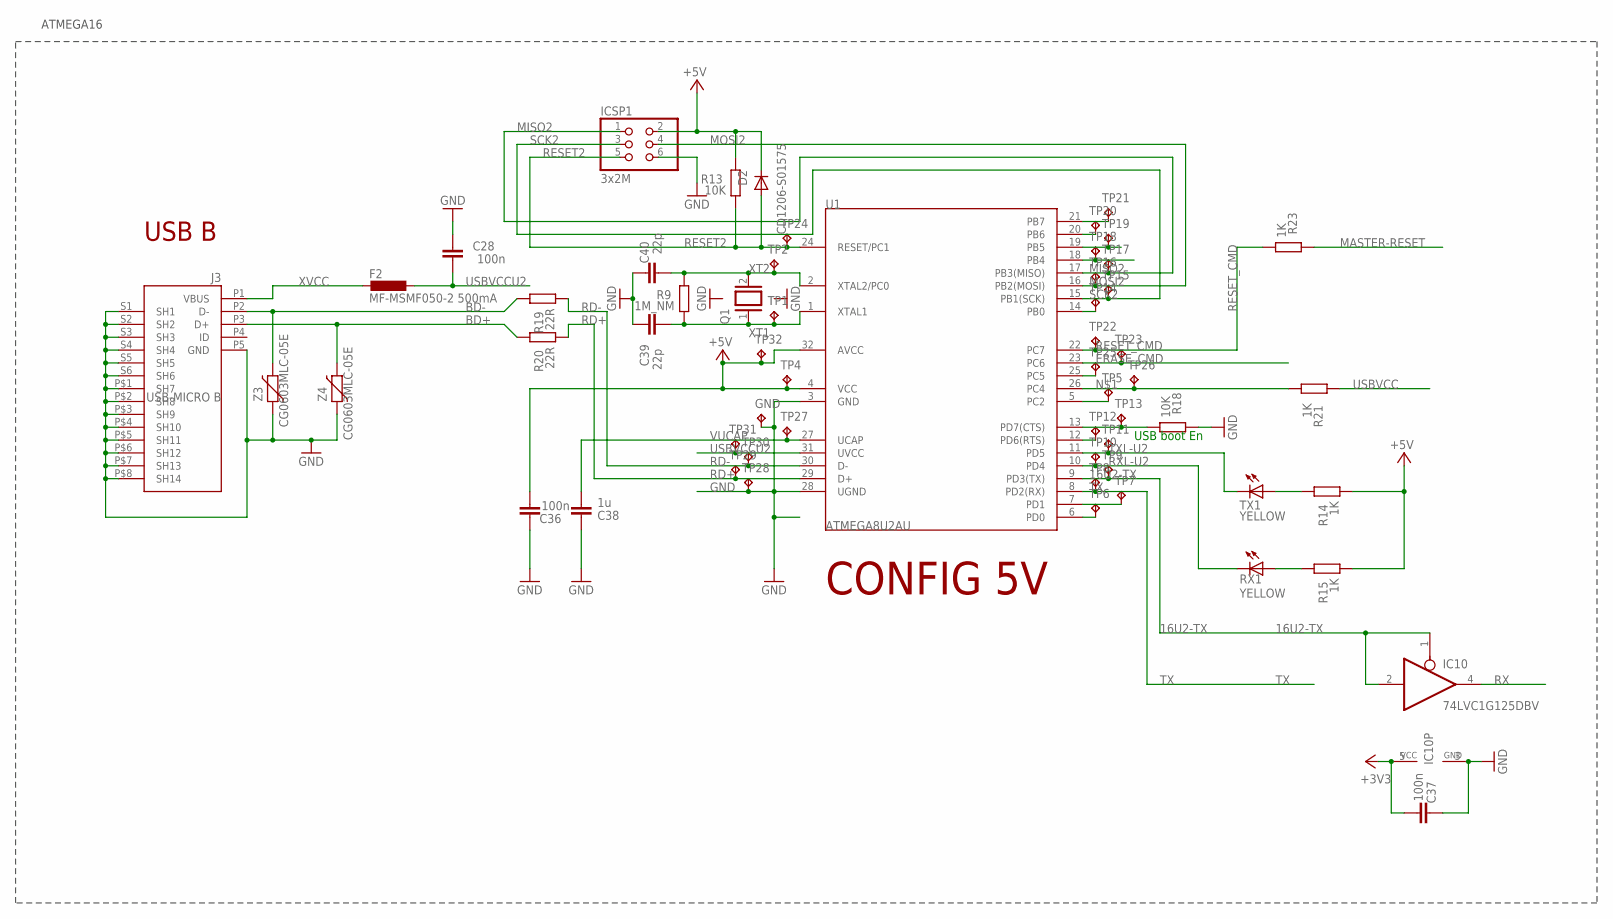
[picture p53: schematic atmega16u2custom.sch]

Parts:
C28, C36, C37: 100n; C0805
C38: 1u; C0805
C39, C40: 22p; C0805
D2: CD1206-S01575; MINIMELF
F2: MF-MSMF050-2 500mA; L1812
GND: TPB1,27; B1,27
IC10: 74LVC1G125DBV; SOT23-5
ICSP1: 3x2M; 2X03
J3: USB-MICRO B; CON2_USB_MICRO_B_AT
Q1: XTAL/S; QS
R9: 1M_NM; R0805
R13, R18: 10K; R0805
R14, R15, R21, R23: 1K; R0805
R19, R20: 22R; R0805
RX1: YELLOW; CHIP-LED0805
TP1, TP2, TP4, TP5, TP6, TP7, TP8, TP9, TP10, TP11, TP12, TP13, TP14, TP15, TP16, TP17, TP18, TP19, TP20, TP21, TP22, TP23, TP24, TP25, TP26, TP27, TP28, TP29, TP30, TP31, TP32: TPB1,27; B1,27
TX1: YELLOW; CHIP-LED0805
U1: ATMEGA8U2AU; TQFP32-08
Z3, Z4: CG0603MLC-05E; CT/CN0603

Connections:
8PB4: TP18.TP, U1.18 (PB4)
8PB5: TP19.TP, U1.19 (PB5)
8PB6: TP20.TP, U1.20 (PB6)
16U2-TX: IC10.1 (OE), IC10.2 (I), TP9.TP, U1.9 (PD3(TX))
+3V3: C37.1, IC10.5 (VCC)
+5V: C36.1, D2.C, ICSP1.2, R13.2, R14.1, R15.1, TP4.TP, TP32.TP, U1.4 (VCC), U1.32 (AVCC)
BD+: J3.P3 (D+), R20.2, Z4.2
BD-: J3.P2 (D-), R19.2, Z3.2
DTR: R18.1, TP13.TP, U1.13 (PD7(CTS))
ERASE_CMD: TP23.TP, U1.23 (PC6)
GND: C28.2, C36.2, C37.2, C38.2, C39.2, C40.2, GND.TP, IC10.3 (GND), ICSP1.6, J3.P5 (GND), J3.P$1 (SH7), J3.P$2 (SH8), J3.P$3 (SH9), J3.P$4 (SH10), J3.P$5 (SH11), J3.P$6 (SH12), J3.P$7 (SH13), J3.P$8 (SH14), J3.S1 (SH1), J3.S2 (SH2), J3.S3 (SH3), J3.S4 (SH4), J3.S5 (SH5), J3.S6 (SH6), R18.2, TP28.TP, U1.3 (GND), U1.28 (UGND), Z3.1, Z4.1
MASTER-RESET: R23.2
MISO2: ICSP1.1, TP17.TP, U1.17 (PB3(MISO))
MOSI2: ICSP1.4, TP16.TP, U1.16 (PB2(MOSI))
unnamed: R21.1, TP26.TP, U1.26 (PC4)
unnamed: TP5.TP, U1.5 (PC2)
unnamed: TP6.TP, U1.6 (PD0)
unnamed: R15.2, RX1.A
unnamed: TP7.TP, U1.7 (PD1)
unnamed: TP12.TP, U1.12 (PD6(RTS))
unnamed: TP25.TP, U1.25 (PC5)
unnamed: TP14.TP, U1.14 (PB0)
unnamed: TP21.TP, U1.21 (PB7)
unnamed: R14.2, TX1.A
RD+: R20.1, TP29.TP, U1.29 (D+)
RD-: R19.1, TP30.TP, U1.30 (D-)
RESET2: D2.A, ICSP1.5, R13.1, TP24.TP, U1.24 (RESET/PC1)
RESET_CMD: R23.1, TP22.TP, U1.22 (PC7)
RX: IC10.4 (O)
RXL-U2: RX1.C, TP10.TP, U1.10 (PD4)
SCK2: ICSP1.3, TP15.TP, U1.15 (PB1(SCK))
TX: TP8.TP, U1.8 (PD2(RX))
TXL-U2: TP11.TP, TX1.C, U1.11 (PD5)
USBVCC: R21.2
USBVCCU2: C28.1, F2.1, TP31.TP, U1.31 (UVCC)
VUCAP: C38.1, TP27.TP, U1.27 (UCAP)
XT1: C39.1, Q1.1, R9.1, TP1.TP, U1.1 (XTAL1)
XT2: C40.1, Q1.2, R9.2, TP2.TP, U1.2 (XTAL2/PC0)
XVCC: F2.2, J3.P1 (VBUS)

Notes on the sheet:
USB boot En
CONFIG 5V
USB B
ATMEGA16

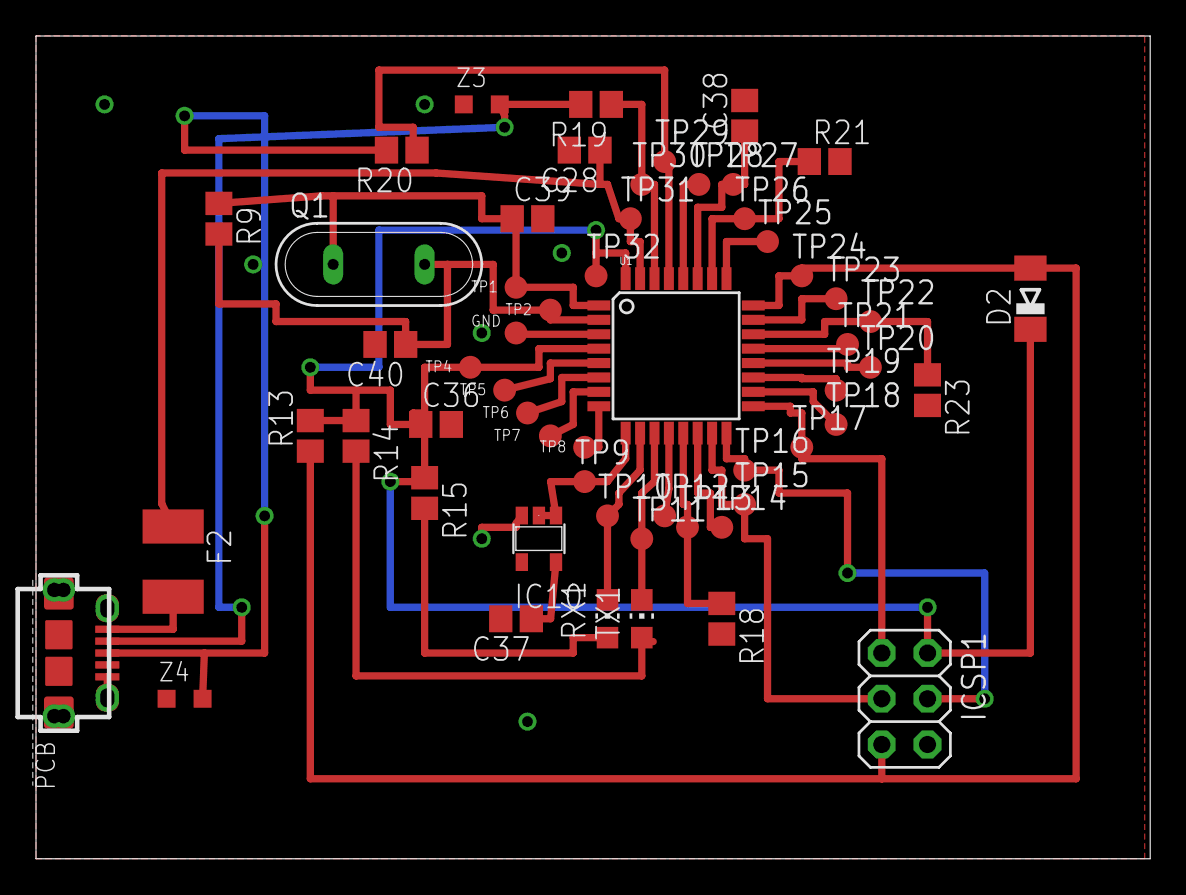
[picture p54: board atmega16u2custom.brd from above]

Board: 2 copper layers, 61.9 x 45.7 mm, 58 parts (0 on the bottom side), 36 nets.

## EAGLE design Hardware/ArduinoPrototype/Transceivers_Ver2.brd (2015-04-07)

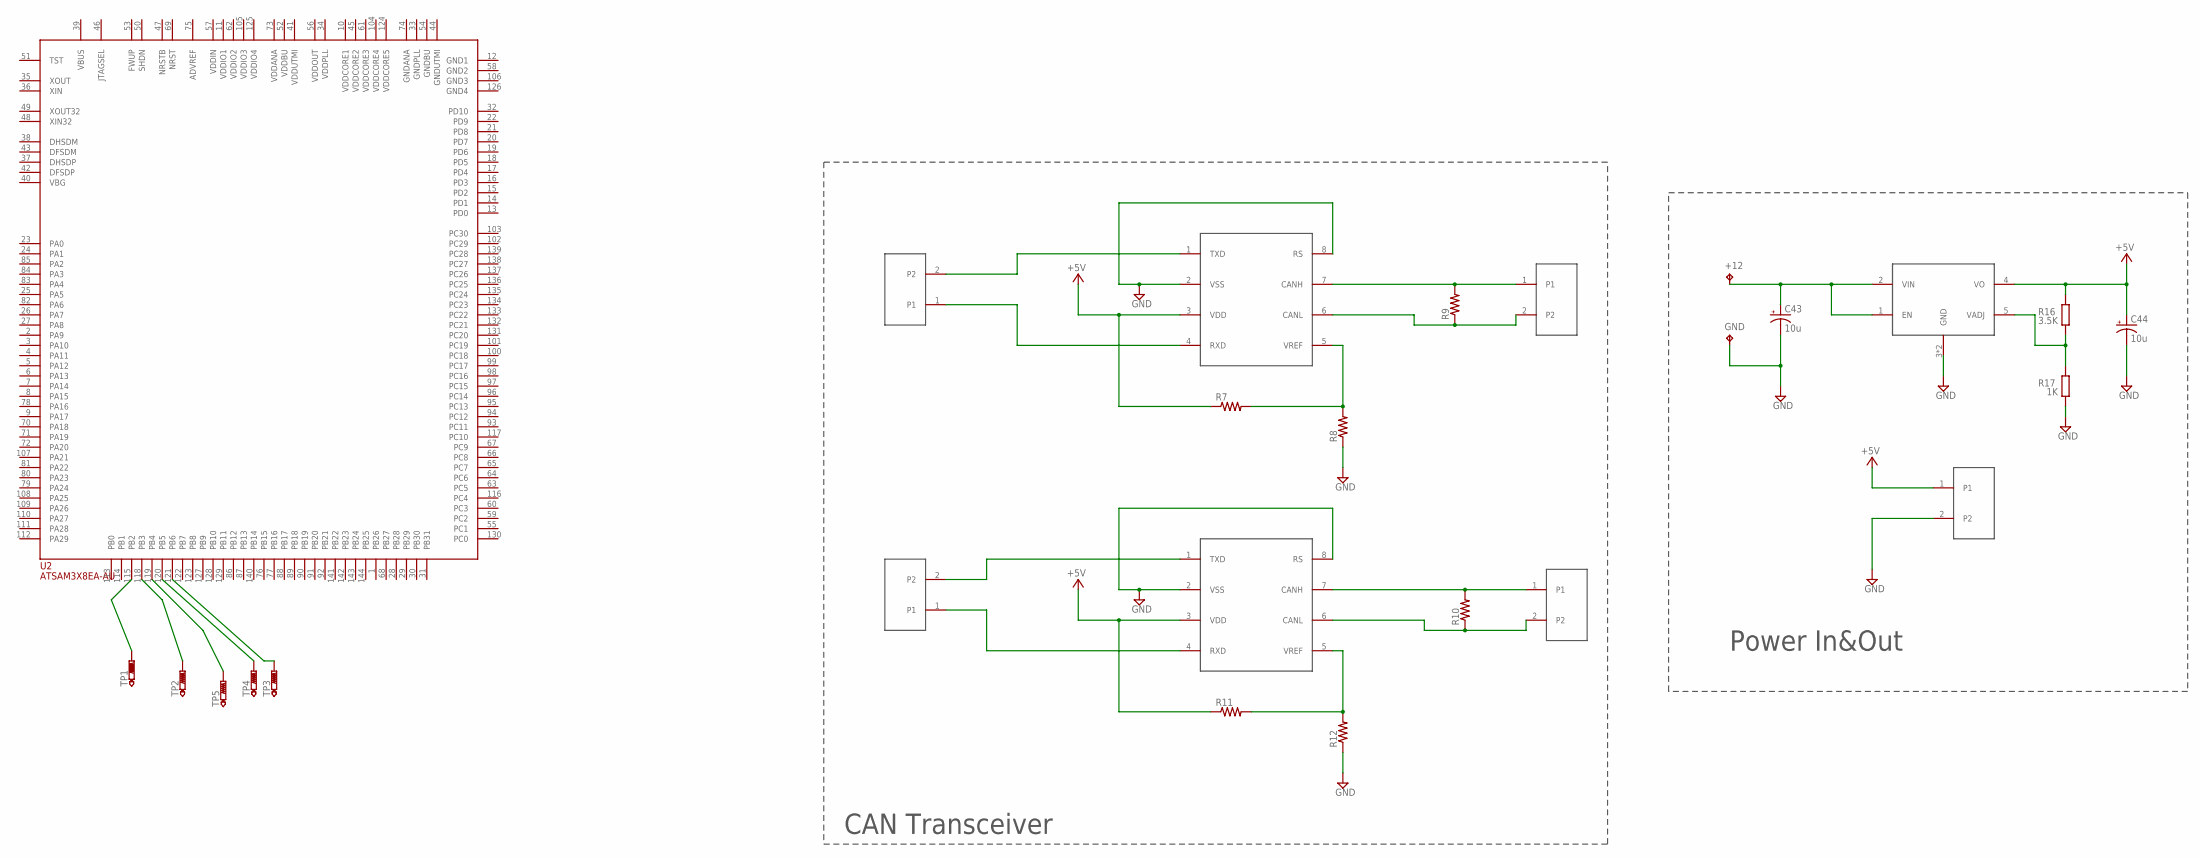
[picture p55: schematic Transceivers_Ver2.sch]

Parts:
+12: TPPAD1-13; P1-13
C43, C44: 10u; 153CLV-0405
CAN0, CAN1: CON-100MIL; 2X1-100MIL
GND: TPPAD1-13; P1-13
POWER: CON-100MIL; 2X1-100MIL
R7, R8, R9, R10, R11, R12: R-US_R0805; R0805
R16: 3.5K; R0805
R17: 1K; R0805
TP1, TP2, TP3, TP4, TP5: PTR1PAD1-13Y; P1-13Y
TXRX0, TXRX1: CON-100MIL; 2X1-100MIL
U1, U4: MCP2551; SOIC8
U2: ATSAM3X8EA-AU; LQFP144
U5: TLF1963TBATMA1; DPAK

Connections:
+5V: C44.+, POWER.1, R7.1, R11.1, R16.2, U1.3 (VDD), U4.3 (VDD), U5.4 (VO)
ADVREF: U2.75 (ADVREF)
CH0: CAN0.1, R9.2, U1.7 (CANH)
CH1: CAN1.1, R10.2, U4.7 (CANH)
CL0: CAN0.2, R9.1, U1.6 (CANL)
CL1: CAN1.2, R10.1, U4.6 (CANL)
GND: C43.-, C44.-, GND.TP, POWER.2, R8.1, R12.1, R17.1, U1.2 (VSS), U1.8 (RS), U4.2 (VSS), U4.8 (RS), U5.3 (GND), U5.6 (GND)
GND1: U2.12 (GND1)
GND2: U2.58 (GND2)
GND3: U2.106 (GND3)
GND4: U2.126 (GND4)
GNDANA: U2.74 (GNDANA)
GNDBU: U2.54 (GNDBU)
GNDPLL: U2.33 (GNDPLL)
GNDUTMI: U2.44 (GNDUTMI)
unnamed: TP1.TP, U2.115 (PB2)
unnamed: TP2.TP, U2.118 (PB3)
unnamed: R7.2, R8.2, U1.5 (VREF)
unnamed: TP5.TP, U2.119 (PB4)
unnamed: TP4.TP, U2.120 (PB5)
unnamed: TP3.TP, U2.121 (PB6)
unnamed: R11.2, R12.2, U4.5 (VREF)
unnamed: +12.TP, C43.+, U5.1 (EN), U5.2 (VIN)
unnamed: R16.1, R17.2, U5.5 (VADJ)
RX0: TXRX0.1, U1.4 (RXD)
RX1: TXRX1.1, U4.4 (RXD)
TX0: TXRX0.2, U1.1 (TXD)
TX1: TXRX1.2, U4.1 (TXD)
VBUS: U2.39 (VBUS)
VDDANA: U2.73 (VDDANA)
VDDBU: U2.52 (VDDBU)
VDDIN: U2.57 (VDDIN)
VDDIO1: U2.11 (VDDIO1)
VDDIO2: U2.62 (VDDIO2)
VDDIO3: U2.105 (VDDIO3)
VDDIO4: U2.125 (VDDIO4)

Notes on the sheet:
CAN Transceiver
Power In&Out

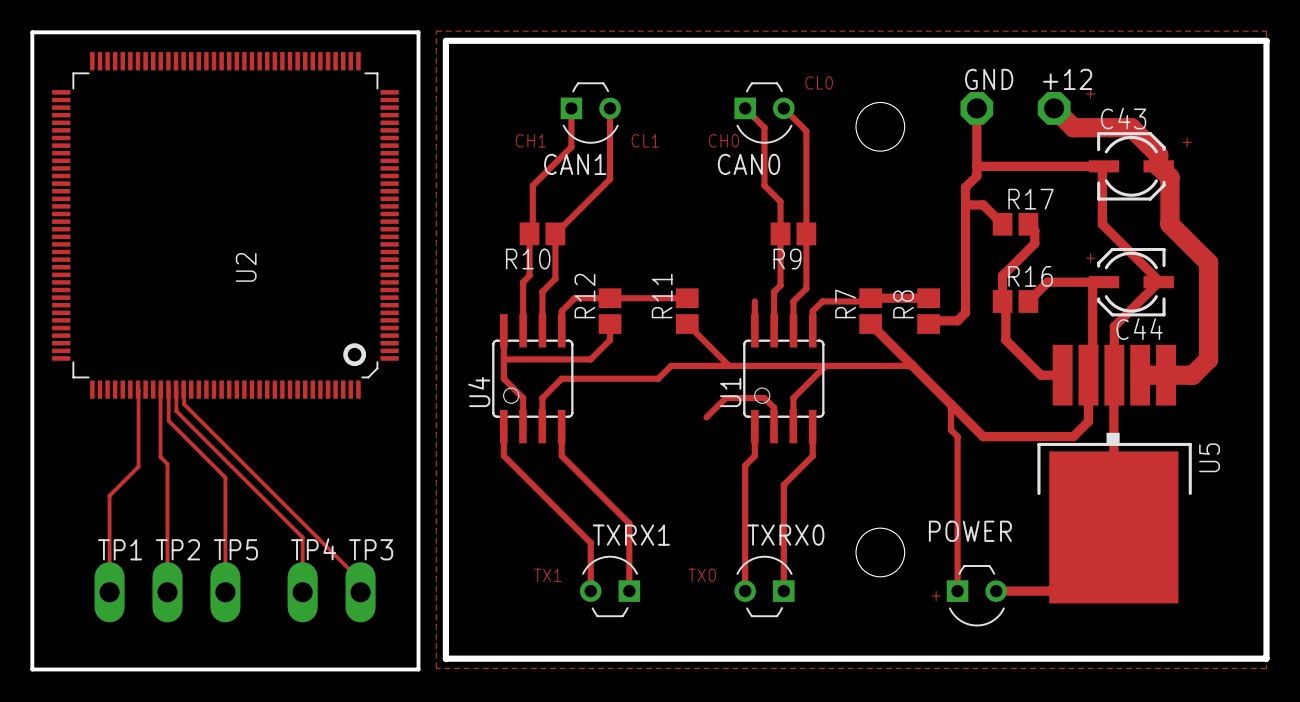
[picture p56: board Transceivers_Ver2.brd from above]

Board: 2 copper layers, 81.2 x 41.9 mm, 26 parts (0 on the bottom side), 19 nets.

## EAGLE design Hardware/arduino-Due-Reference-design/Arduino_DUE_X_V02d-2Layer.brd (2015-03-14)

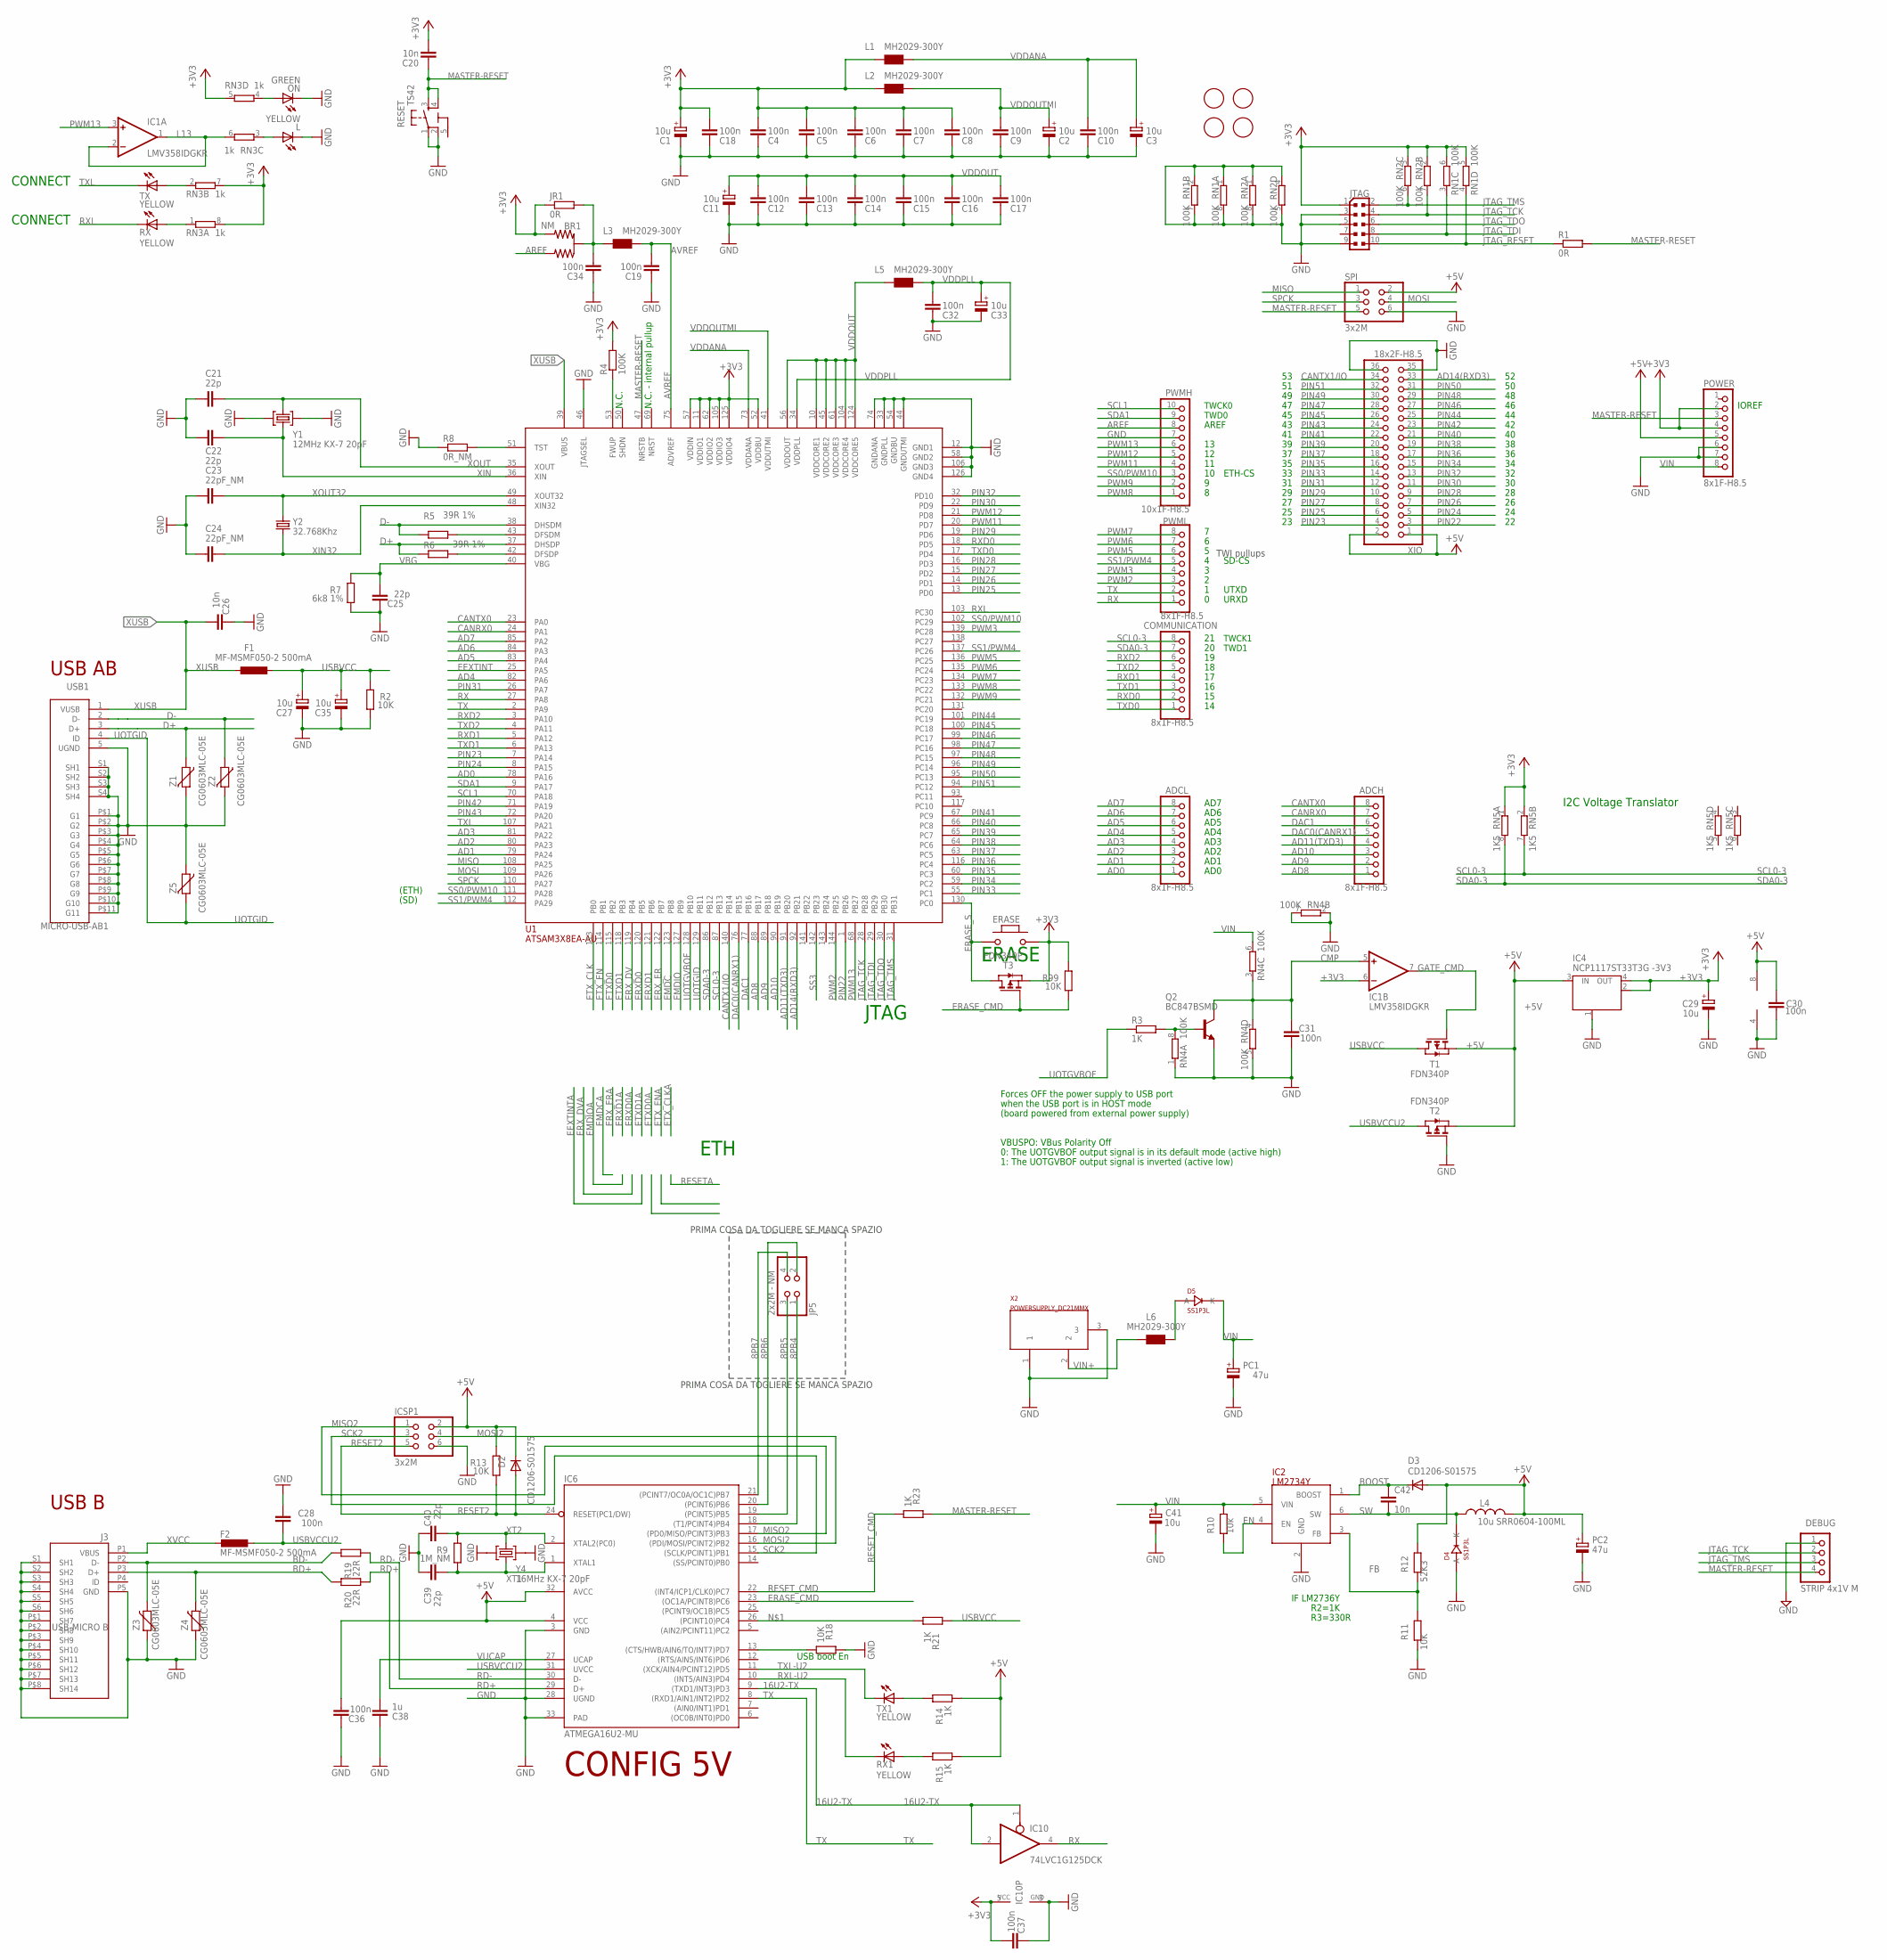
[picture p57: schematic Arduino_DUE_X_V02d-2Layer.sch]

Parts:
ADCH: 8x1F-H8.5; 1X08
ADCL: 8x1F-H8.5; 1X08
BR1: NM; J0402
C1, C2, C3, C11, C27, C29, C33, C35, C41: 10u; SMC_B
C4, C5, C6, C7, C8, C9, C10, C12, C13, C14, C15, C16, C17, C18, C19, C28, C30, C31, C32, C34, C36, C37: 100n; C0402
C20, C26: 10n; C0402
C21, C22, C25, C39, C40: 22p; C0402
C23, C24: 22pF_NM; C0402
C38: 1u; C0402
C42: 10n; C0603-ROUND
COMMUNICATION: 8x1F-H8.5; 1X08
D2, D3: CD1206-S01575; MINIMELF
D4, D5: SS1P3L; DO220AAL
DEBUG: STRIP 4x1V M; 1X04
ERASE: MYSMD_PB157; SMD_157SW
F1, F2: MF-MSMF050-2 500mA; L1812
FID1, FID2, FID3, FID4: FIDUCIALMOUNT; FIDUCIA-MOUNT
IC1: LMV358IDGKR; MSOP08
IC2: LM2734Y; SOT23-6
IC4: NCP1117ST33T3G -3V3; SOT223
IC6: ATMEGA16U2-MU; MLF32
IC10: 74LVC1G125DCK; SC70-5
ICSP1: 3x2M; 2X03
J3: USB-MICRO B; CON2_USB_MICRO_B_AT
JP5: 2x2M - NM; 2X02
JR1: 0R; R0402
JTAG: PINHEAD_PINHD-2X5PASSO127; PINHEAD_2X05_127
L: YELLOW; CHIP-LED0805
L1, L2, L3, L5, L6: MH2029-300Y; 0805
L4: 10u SRR0604-100ML; SRR0604
ON: GREEN; CHIP-LED0805
PC1, PC2: 47u; PANASONIC_D
POWER: 8x1F-H8.5; 1X08
PWMH: 10x1F-H8.5; 1X10
PWML: 8x1F-H8.5; 1X08
Q2: BC847BSMD; SOT23
R1: 0R; R0402
R2, R13, R18, R99: 10K; R0402
R3, R14, R15, R21, R23: 1K; R0402
R4: 100K; R0402
R5, R6: 39R 1%; R0402
R7: 6k8 1%; R0603-ROUND
R8: 0R_NM; R0402
R9: 1M_NM; R0402
R10: 10k; R0402
R11: 10K; R0603-ROUND
R12: 52K3; R0603-ROUND
R19, R20: 22R; R0402
RESET: TS42
RN1, RN2, RN4: 100K; CAT16
RN3: 1k; CAY16
RN5: 1K5; CAT16
RX, RX1: YELLOW; CHIP-LED0805
SPI: 3x2M; 2X03
T1, T2, T3: FDN340P; SOT-23
TX, TX1: YELLOW; CHIP-LED0805
U1: ATSAM3X8EA-AU; LQFP144
USB1: MICRO-USB-AB1; MCR-AB1-S-RA-SMT
X2: POWERSUPPLY_DC21MMX; POWERSUPPLY_DC-21MM
XIO: 18x2F-H8.5; 2X18
Y1: 12MHz KX-7 20pF; CRYSTAL-3.2-2.5
Y2: 32.768Khz; RESONATOR_EPSON_FC_145
Y4: 16MHz KX-7 20pF; CRYSTAL-3.2-2.5
Z1, Z2, Z3, Z4, Z5: CG0603MLC-05E; CT/CN0603

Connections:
5-GND: RESET.5 (5-GND)
8PB4: IC6.18 ((T1/PCINT4)PB4), JP5.1
8PB5: IC6.19 ((PCINT5)PB5), JP5.3
8PB6: IC6.20 ((PCINT6)PB6), JP5.2
8PB7: IC6.21 ((PCINT7/OC0A/OC1C)PB7), JP5.4
16U2-TX: IC6.9 ((TXD1/INT3)PD3), IC10.1 (OE), IC10.2 (I)
+3V3: BR1.3 (2), C1.+, C4.2, C5.2, C6.2, C7.2, C8.2, C18.2, C20.2, C29.+, C37.1, ERASE.1, IC1.6 (-IN), IC4.2 (OUT), IC4.4 (OUT), IC10.5 (VCC), JR1.1, JTAG.1, L1.1, L2.1, POWER.2, POWER.4, R4.2, R99.2, RN1.5 (2), RN1.6 (2), RN2.2 (1), RN2.3 (1), RN3.5 (2), RN3.7 (2), RN3.8 (2), RN5.1, RN5.2 (1), T3.2 (S), U1.11 (VDDIO1), U1.52 (VDDBU), U1.57 (VDDIN), U1.62 (VDDIO2), U1.105 (VDDIO3), U1.125 (VDDIO4)
+5V: C30.2, C36.1, D2.C, D3.A, IC1.8 (V+), IC4.3 (IN), IC6.4 (VCC), IC6.32 (AVCC), ICSP1.2, L4.P$2 (2), PC2.+, POWER.5, R12.1, R13.2, R14.1, R15.1, SPI.2, T1.2 (S), T2.2 (S), XIO.1, XIO.2
AD0: ADCL.1, U1.78 (PA16)
AD1: ADCL.2, U1.79 (PA24)
AD2: ADCL.3, U1.80 (PA23)
AD3: ADCL.4, U1.81 (PA22)
AD4: ADCL.5, U1.82 (PA6)
AD5: ADCL.6, U1.83 (PA4)
AD6: ADCL.7, U1.84 (PA3)
AD7: ADCL.8, U1.85 (PA2)
AD8: ADCH.1, U1.88 (PB17)
AD9: ADCH.2, U1.89 (PB18)
AD10: ADCH.3, U1.90 (PB19)
AD11(TXD3): ADCH.4, U1.91 (PB20)
AD14(RXD3): U1.92 (PB21), XIO.33
AREF: BR1.1, PWMH.8
AVREF: C19.2, L3.2, U1.75 (ADVREF)
AVREFL: BR1.2 (C), C34.2, JR1.2, L3.1
BD+: J3.P3 (D+), R20.2, Z4.2
BD-: J3.P2 (D-), R19.2, Z3.2
BOOST: C42.1, D3.C, IC2.1 (BOOST)
CANRX0: ADCH.7, U1.24 (PA1)
CANTX0: ADCH.8, U1.23 (PA0)
CANTX1/IO: U1.140 (PB14), XIO.34
CMP: C31.2, IC1.5 (+IN), Q2.3 (C), RN4.3 (1), RN4.4 (1)
D+: R6.1, U1.37 (DHSDP), USB1.3 (D+), Z1.1
D-: R5.1, U1.38 (DHSDM), USB1.2 (D-), Z2.1
DAC0(CANRX1): ADCH.5, U1.76 (PB15)
DAC1: ADCH.6, U1.77 (PB16)
DTR: IC6.13 ((CTS/HWB/AIN6/TO/INT7)PD7), R18.1
EEXTINT: U1.25 (PA5)
EMDC: U1.123 (PB8)
EMDIO: U1.127 (PB9)
EN: IC2.4 (EN), R10.2
ERASE_CMD: IC6.23 ((OC1A/PCINT8)PC6), R99.1, T3.3 (G)
ERASE_S: ERASE.2, T3.1 (D), U1.130 (PC0)
ERXD0: U1.120 (PB5)
ERXD1: U1.121 (PB6)
ERX_DV: U1.119 (PB4)
ERX_ER: U1.122 (PB7)
ETXD0: U1.115 (PB2)
ETXD1: U1.118 (PB3)
ETX_CLK: U1.113 (PB0)
ETX_EN: U1.114 (PB1)
FB: IC2.3 (FB), R11.1, R12.2
GATE_CMD: IC1.7 (OUT), T1.3 (G)
GND: C1.-, C2.-, C3.-, C4.1, C5.1, C6.1, C7.1, C8.1, C9.1, C10.1, C11.-, C12.1, C13.1, C14.1, C15.1, C16.1, C17.1, C18.1, C19.1, C21.2, C22.2, C23.2, C24.2, C25.2, C26.2, C27.-, C28.2, C29.-, C30.1, C31.1, C32.1, C33.-, C34.1, C35.-, C36.2, C37.2, C38.2, C39.2, C40.2, C41.-, D4.P$2 (A), DEBUG.1, IC1.4 (V-), IC2.2 (GND), IC4.1 (GND/ADJ), IC6.3 (GND), IC6.28 (UGND), IC6.33 (PAD), IC10.3 (GND), ICSP1.6, J3.P5 (GND), J3.P$1 (SH7), J3.P$2 (SH8), J3.P$3 (SH9), J3.P$4 (SH10), J3.P$5 (SH11), J3.P$6 (SH12), J3.P$7 (SH13), J3.P$8 (SH14), J3.S1 (SH1), J3.S2 (SH2), J3.S3 (SH3), J3.S4 (SH4), J3.S5 (SH5), J3.S6 (SH6), JTAG.3, JTAG.5, JTAG.9, L.C, ON.C, PC1.-, PC2.-, POWER.6, POWER.7, PWMH.7, Q2.2 (E), R2.1, R7.1, R8.1, R11.2, R18.2, RESET.1, RESET.2, RN1.1, RN1.2 (1), RN1.7 (2), RN1.8 (2), RN2.1, RN2.4 (1), RN2.5 (2), RN2.8 (2), RN4.1, RN4.2 (1), RN4.5 (2), RN4.7 (2), SPI.6, T2.3 (G), U1.12 (GND1), U1.33 (GNDPLL), U1.44 (GNDUTMI), U1.46 (JTAGSEL), U1.54 (GNDBU), U1.58 (GND2), U1.74 (GNDANA), U1.106 (GND3), U1.126 (GND4), USB1.5 (UGND), USB1.P$1 (G1), USB1.P$2 (G2), USB1.P$3 (G3), USB1.P$4 (G4), USB1.P$5 (G5), USB1.P$6 (G6), USB1.P$7 (G7), USB1.P$8 (G8), USB1.P$9 (G9), USB1.P$10 (G10), USB1.P$11 (G11), USB1.S1 (SH1), USB1.S2 (SH2), USB1.S3 (SH3), USB1.S4 (SH4), X2.1, X2.3, XIO.35, XIO.36, Y1.2 (GND), Y1.4 (GND), Y4.2 (GND), Y4.4 (GND), Z1.2, Z2.2, Z3.1, Z4.1, Z5.1
JTAG_RESET: JTAG.10, R1.1, RN1.4 (1)
JTAG_TCK: DEBUG.2, JTAG.4, RN2.7 (2), U1.28 (PB28)
JTAG_TDI: JTAG.8, RN1.3 (1), U1.29 (PB29)
JTAG_TDO: JTAG.6, U1.30 (PB30)
JTAG_TMS: DEBUG.3, JTAG.2, RN2.6 (2), U1.31 (PB31)
L13: IC1.1 (OUT), IC1.2 (-IN), RN3.6 (2)
MASTER-RESET: C20.1, DEBUG.4, POWER.3, R1.2, R23.2, RESET.3, RESET.4, SPI.5, U1.47 (NRSTB)
MISO: SPI.1, U1.108 (PA25)
MISO2: IC6.17 ((PD0/MISO/PCINT3)PB3), ICSP1.1
MOSI: SPI.4, U1.109 (PA26)
MOSI2: IC6.16 ((PDI/MOSI/PCINT2)PB2), ICSP1.4
unnamed: IC6.26 ((PCINT10)PC4), R21.1
unnamed: L.A, RN3.3 (1)
unnamed: ON.A, RN3.4 (1)
unnamed: R15.2, RX1.A
unnamed: R8.2, U1.51 (TST)
unnamed: Q2.1 (B), R3.2, RN4.8 (2)
unnamed: R4.1, U1.53 (FWUP)
unnamed: D5.P$2 (A), L6.1
unnamed: R5.2, U1.43 (DFSDM)
unnamed: R6.2, U1.42 (DFSDP)
unnamed: R14.2, TX1.A
unnamed: RN3.1, RX.A
unnamed: RN3.2 (1), TX.A
PIN22: U1.1 (PB26), XIO.3
PIN23: U1.7 (PA14), XIO.4
PIN24: U1.8 (PA15), XIO.5
PIN25: U1.13 (PD0), XIO.6
PIN26: U1.14 (PD1), XIO.7
PIN27: U1.15 (PD2), XIO.8
PIN28: U1.16 (PD3), XIO.9
PIN29: U1.19 (PD6), XIO.10
PIN30: U1.22 (PD9), XIO.11
PIN31: U1.26 (PA7), XIO.12
PIN32: U1.32 (PD10), XIO.13
PIN33: U1.55 (PC1), XIO.14
PIN34: U1.59 (PC2), XIO.15
PIN35: U1.60 (PC3), XIO.16
PIN36: U1.116 (PC4), XIO.17
PIN37: U1.63 (PC5), XIO.18
PIN38: U1.64 (PC6), XIO.19
PIN39: U1.65 (PC7), XIO.20
PIN40: U1.66 (PC8), XIO.21
PIN41: U1.67 (PC9), XIO.22
PIN42: U1.71 (PA19), XIO.23
PIN43: U1.72 (PA20), XIO.24
PIN44: U1.101 (PC19), XIO.25
PIN45: U1.100 (PC18), XIO.26
PIN46: U1.99 (PC17), XIO.27
PIN47: U1.98 (PC16), XIO.28
PIN48: U1.97 (PC15), XIO.29
PIN49: U1.96 (PC14), XIO.30
PIN50: U1.95 (PC13), XIO.31
PIN51: U1.94 (PC12), XIO.32
PWM2: PWML.3, U1.144 (PB25)
PWM3: PWML.4, U1.139 (PC28)
PWM5: PWML.6, U1.136 (PC25)
PWM6: PWML.7, U1.135 (PC24)
PWM7: PWML.8, U1.134 (PC23)
PWM8: PWMH.1, U1.133 (PC22)
PWM9: PWMH.2, U1.132 (PC21)
PWM11: PWMH.4, U1.20 (PD7)
PWM12: PWMH.5, U1.21 (PD8)
PWM13: IC1.3 (+IN), PWMH.6, U1.68 (PB27)
RD+: IC6.29 (D+), R20.1
RD-: IC6.30 (D-), R19.1
RESET2: D2.A, IC6.24 (RESET(PC1/DW)), ICSP1.5, R13.1
RESET_CMD: IC6.22 ((INT4/ICP1/CLK0)PC7), R23.1
RX: IC10.4 (O), PWML.1, U1.27 (PA8)
RXD0: COMMUNICATION.2, U1.18 (PD5)
RXD1: COMMUNICATION.4, U1.5 (PA12)
RXD2: COMMUNICATION.6, U1.3 (PA10)
RXL: RX.C, U1.103 (PC30)
RXL-U2: IC6.10 ((INT5/AIN3)PD4), RX1.C
SCK2: IC6.15 ((SCLK/PCINT1)PB1), ICSP1.3
SCL0-3: COMMUNICATION.8, RN5.7 (2), U1.87 (PB13)
SCL1: PWMH.10, U1.70 (PA18)
SDA0-3: COMMUNICATION.7, RN5.8 (2), U1.86 (PB12)
SDA1: PWMH.9, U1.9 (PA17)
SPCK: SPI.3, U1.110 (PA27)
SS0/PWM10: PWMH.3, U1.102 (PC29), U1.111 (PA28)
SS1/PWM4: PWML.5, U1.112 (PA29), U1.137 (PC26)
SS3: U1.142 (PB23)
SW: C42.2, D4.P$1 (K), IC2.6 (SW), L4.P$1 (1)
TX: IC6.8 ((RXD1/AIN1/INT2)PD2), PWML.2, U1.2 (PA9)
TXD0: COMMUNICATION.1, U1.17 (PD4)
TXD1: COMMUNICATION.3, U1.6 (PA13)
TXD2: COMMUNICATION.5, U1.4 (PA11)
TXL: TX.C, U1.107 (PA21)
TXL-U2: IC6.11 ((XCK/AIN4/PCINT12)PD5), TX1.C
UOTGID: U1.129 (PB11), USB1.4 (ID), Z5.2
UOTGVBOF: R3.1, U1.128 (PB10)
USBVCC: C27.+, C35.+, F1.1, R2.2, R21.2, T1.1 (D)
USBVCCU2: C28.1, F2.1, IC6.31 (UVCC), T2.1 (D)
VBG: C25.1, R7.2, U1.40 (VBG)
VDDANA: C3.+, C10.2, L1.2, U1.73 (VDDANA)
VDDOUT: C11.+, C12.2, C13.2, C14.2, C15.2, C16.2, C17.2, L5.1, U1.10 (VDDCORE1), U1.45 (VDDCORE2), U1.56 (VDDOUT), U1.61 (VDDCORE3), U1.104 (VDDCORE4), U1.124 (VDDCORE5)
VDDOUTMI: C2.+, C9.2, L2.2, U1.41 (VDDUTMI)
VDDPLL: C32.2, C33.+, L5.2, U1.34 (VDDPLL)
VIN: C41.+, D5.P$1 (K), IC2.5 (VIN), PC1.+, POWER.8, R10.1, RN4.6 (2)
VIN+: L6.2, X2.2
VUCAP: C38.1, IC6.27 (UCAP)
XIN: C22.1, U1.36 (XIN), Y1.1 (C1)
XIN32: C24.1, U1.48 (XIN32), Y2.P$2 (2)
XOUT: C21.1, U1.35 (XOUT), Y1.3 (C2)
XOUT32: C23.1, U1.49 (XOUT32), Y2.P$1 (1)
XT1: C39.1, IC6.1 (XTAL1), R9.1, Y4.1 (C1)
XT2: C40.1, IC6.2 (XTAL2(PC0)), R9.2, Y4.3 (C2)
XUSB: C26.1, F1.2, U1.39 (VBUS), USB1.1 (VUSB)
XVCC: F2.2, J3.P1 (VBUS)

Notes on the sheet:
TWI pullups
TWCK1
TWD1
IOREF
TWCK0
TWD0
AD1
AD2
AD3
AD4
AD5
AD6
AD0
USB AB
AREF
AD7
SD-CS
Forces OFF the power supply to USB port
when the USB port is in HOST mode
(board powered from external power supply)
N.C.
JTAG
ERASE
CONNECT
VBUSPO: VBus Polarity Off
0: The UOTGVBOF output signal is in its default mode (active high)
1: The UOTGVBOF output signal is inverted (active low)
ETH
UTXD
URXD
(ETH)
(SD)
ETH-CS
I2C Voltage Translator
USB boot En
IF LM2736Y
R2=1K
R3=330R
PRIMA COSA DA TOGLIERE SE MANCA SPAZIO
CONFIG 5V

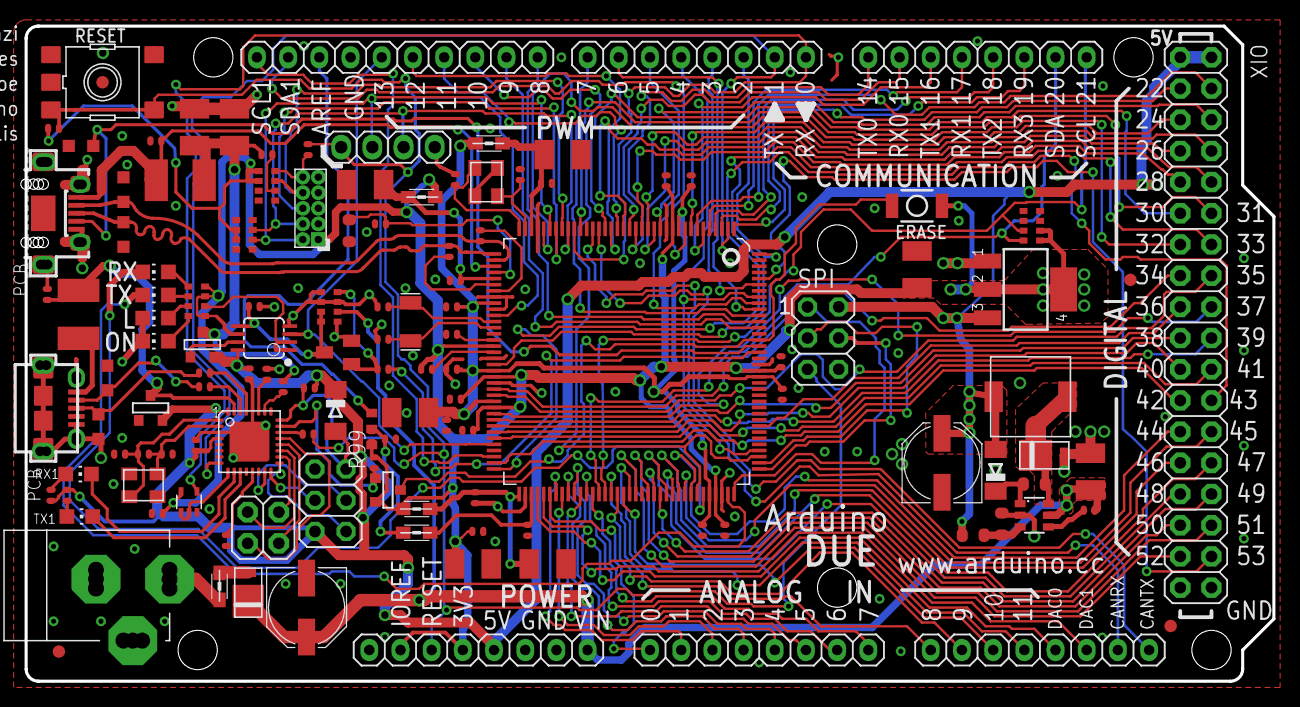
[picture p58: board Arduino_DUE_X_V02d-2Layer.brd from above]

Board: 2 copper layers, 101.6 x 53.3 mm, 129 parts (0 on the bottom side), 150 nets.

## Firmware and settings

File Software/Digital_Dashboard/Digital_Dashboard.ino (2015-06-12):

// Digital Dash - Capstone 2015
// Sean Koppenhafer, Chad Thueson, Jaime Rodriguez, Rishal Dass and Noah Erickson
//
// Digital Dashboard main file
//
// Uses due_can library from https://github.com/collin80/due_can

#include <genieArduino.h>
#include <Arduino.h>
#include <due_can.h>
#include "Digital_Dashboard.h"
#include "CAN0.h"
#include "CAN1.h"

CAN_FRAME message;
screen_msgs screen_messages;
warning_msgs warning_messages;
Genie genie;

#define RESETLINE 4  //Change this if you are not using Arduino Adaptor Shield Version 2 (SEE CODE BELOW)

void setup() {
  Can0.begin(CAN_BPS_1000K);  //CAN0 receives RMS messages
  Can1.begin(CAN_BPS_500K);  //CAN1 receives BMS messages

  pinMode(IMD_BUTTON, INPUT);

  //Initialize serial for the screen
  Serial.begin(115200);
  genie.Begin(Serial);

  //Setup for the screen
  pinMode(RESETLINE, OUTPUT);  // Set D4 on Arduino to Output (4D Arduino Adaptor V2 - Display Reset)
  digitalWrite(RESETLINE, 1);  // Reset the Display via D4
  delay(100);
  digitalWrite(RESETLINE, 0);  // unReset the Display via D4
  delay (3500); //let the display start up after the reset (This is important)

  //Turn the Display on (Contrast)
  genie.WriteContrast(15); // 1 = Display ON, 0 = Display OFF.

  //By default, the due can sets up 7 RX mailboxes and 1 TX mailbox.
  //Since we only care about receiving messages on the screen, we want
  //to make it so that all 8 mailboxes can be used to receive messages.
  Can0.setNumTXBoxes(0);
  setup_CAN0_watches();
  setup_CAN1_watches();
  Can0.setGeneralCallback(CAN0_interrupt_handler);
  Can1.setGeneralCallback(CAN1_interrupt_handler);

  //These functions set the screen struct objects to 0
  init_screen_objects();
  init_screen_structs();
}

void loop() {
  const int IMD_threshold = 500;  //A threshold to signify that the IMD is high (pseudo digital)
  int IMD_level;

#ifdef DISPLAY_SCREEN_OBJECTS
  //Main screen objects
  genie.WriteObject(GENIE_OBJ_ANGULAR_METER, CURRENT_METER_SCREEN_ID, screen_messages.DC_current_value);
  genie.WriteObject(GENIE_OBJ_ANGULAR_METER, MOTOR_TORQUE_METER_SCREEN_ID, screen_messages.motor_torque);
  genie.WriteObject(GENIE_OBJ_TANK, BATTERY_METER_SCREEN_ID, screen_messages.battery_percent);

  //RMS debug screen objects
  genie.WriteObject(GENIE_OBJ_LED_DIGITS, GATE_DRIVER_SCREEN_ID, screen_messages.gate_driver_temp_value);
  genie.WriteObject(GENIE_OBJ_LED_DIGITS, CONTROL_BOARD_SCREEN_ID, screen_messages.control_board_temp_value);
  genie.WriteObject(GENIE_OBJ_LED_DIGITS, MOTOR_TEMP_SCREEN_ID, screen_messages.motor_temp_value);
  genie.WriteObject(GENIE_OBJ_LED_DIGITS, DC_CURRENT_SCREEN_ID, screen_messages.DC_current_value);
  genie.WriteObject(GENIE_OBJ_LED_DIGITS, DC_BUS_VOLTAGE_SCREEN_ID, screen_messages.DC_bus_voltage_value);
  genie.WriteObject(GENIE_OBJ_LED_DIGITS, INTERNAL_VOLTAGE_SCREEN_ID, screen_messages.internal_voltage_value);
  genie.WriteObject(GENIE_OBJ_LED_DIGITS, MOTOR_TORQUE_WARNING_SCREEN_ID, screen_messages.motor_torque);
  
  //Update the RMS state
  if (screen_messages.RMS_state != screen_messages.last_RMS_state) {
    screen_messages.last_RMS_state = screen_messages.RMS_state;
    genie.WriteObject(GENIE_OBJ_STRINGS, RMS_STATE_SCREEN_ID, screen_messages.RMS_state);
  }

  //BMS screen objects
  genie.WriteObject(GENIE_OBJ_LED_DIGITS, RLEC_TEMP_SCREEN_ID, screen_messages.RLEC_temp);
  genie.WriteObject(GENIE_OBJ_LED_DIGITS, MAX_CELL_VOLTAGE_SCREEN_ID, screen_messages.max_cell_voltage);
  genie.WriteObject(GENIE_OBJ_LED_DIGITS, MIN_CELL_VOLTAGE_SCREEN_ID, screen_messages.min_cell_voltage);
  genie.WriteObject(GENIE_OBJ_LED_DIGITS, MIN_CELL_TEMP_SCREEN_ID, screen_messages.min_cell_temp);
  genie.WriteObject(GENIE_OBJ_LED_DIGITS, MAX_CELL_TEMP_SCREEN_ID, screen_messages.max_cell_temp);

  //Warning LEDs - RMS
  //If any of the RMS values are flagged as a warning, then change the screen icon to red
  if (warning_messages.gate_driver_temp_warning || warning_messages.control_board_temp_warning ||
      warning_messages.voltage_12V_warning) {
    genie.WriteObject(GENIE_OBJ_USERIMAGES, RMS_WARNING_IMAGE_SCREEN_ID, WARNING);
  }
  else {
    genie.WriteObject(GENIE_OBJ_USERIMAGES, RMS_WARNING_IMAGE_SCREEN_ID, NO_WARNING);
  }
  genie.WriteObject(GENIE_OBJ_USER_LED, GATE_DRIVER_WARNING_SCREEN_ID, warning_messages.gate_driver_temp_warning);
  genie.WriteObject(GENIE_OBJ_USER_LED, CONTROL_BOARD_WARNING_SCREEN_ID, warning_messages.control_board_temp_warning);
  genie.WriteObject(GENIE_OBJ_USER_LED, WARNING_12V_VOLTAGE_SCREEN_ID, warning_messages.voltage_12V_warning);


  //Warning LEDs - BMS
  //If any of the BMS values are flagged as a warning, then change the screen icon to red
  if (warning_messages.max_cell_voltage_warning || warning_messages.min_cell_voltage_warning ||
      warning_messages.RLEC_temp_warning || warning_messages.max_cell_temp_warning || warning_messages.min_cell_temp_warning) {
    genie.WriteObject(GENIE_OBJ_USERIMAGES, BMS_WARNING_IMAGE_SCREEN_ID, WARNING);
  }
  else {
    genie.WriteObject(GENIE_OBJ_USERIMAGES, BMS_WARNING_IMAGE_SCREEN_ID, NO_WARNING);
  }
  genie.WriteObject(GENIE_OBJ_USER_LED, MAX_CELL_VOLTAGE_WARNING_SCREEN_ID, warning_messages.max_cell_voltage_warning);
  genie.WriteObject(GENIE_OBJ_USER_LED, MIN_CELL_VOLTAGE_WARNING_SCREEN_ID, warning_messages.min_cell_voltage_warning);
  genie.WriteObject(GENIE_OBJ_USER_LED, RLEC_WARNING_TEMP_SCREEN_ID, warning_messages.RLEC_temp_warning);
  genie.WriteObject(GENIE_OBJ_USER_LED, MAX_CELL_TEMP_WARNING_SCREEN_ID, warning_messages.max_cell_temp_warning);
  genie.WriteObject(GENIE_OBJ_USER_LED, MIN_CELL_TEMP_WARNING_SCREEN_ID, warning_messages.min_cell_temp_warning);
#endif

  //Change the IMD icon on the screen to red when there is an IMD error.
  IMD_level = analogRead(IMD_BUTTON);
  if (IMD_level > IMD_threshold) {
    genie.WriteObject(GENIE_OBJ_USERIMAGES, IMD_WARNING_IMAGE_SCREEN_ID, WARNING);
  }
  else {
    genie.WriteObject(GENIE_OBJ_USERIMAGES, IMD_WARNING_IMAGE_SCREEN_ID, NO_WARNING);
  }
}

/******************************************************************************
** CAN0 WATCHES FOR THE CAN MESSAGES NEEDED FROM THE RMS
******************************************************************************/
void setup_CAN0_watches(void) {
  Can0.watchFor(TEMP1_ID);
  Can0.watchFor(TEMP2_ID);
  Can0.watchFor(TEMP3_ID);
  Can0.watchFor(CURRENT_INFO_ID);
  Can0.watchFor(VOLTAGE_INFO_ID);
  Can0.watchFor(INTERNAL_VOLTAGE_ID);
  Can0.watchFor(INTERNAL_STATES_ID);
  Can0.watchFor(MOTOR_TORQUE_ID);
}

/******************************************************************************
** CAN1 WATCHES FOR THE CAN MESSAGES NEEDED FROM THE BMS
******************************************************************************/
void setup_CAN1_watches(void) {
  Can1.watchFor(RLEC4_ID);
  Can1.watchFor(RLEC13_ID);
}

/******************************************************************************
** INIT OBJECTS IN SCREEN DATA STRUCT
** ALL VALUES START OUT AT 0
******************************************************************************/
void init_screen_structs(void) {
  //Warning struct
  warning_messages.gate_driver_temp_warning = 0;
  warning_messages.control_board_temp_warning = 0;
  warning_messages.voltage_12V_warning = 0;
  warning_messages.max_cell_voltage_warning = 0;
  warning_messages.min_cell_voltage_warning = 0;
  warning_messages.RLEC_temp_warning = 0;
  warning_messages.max_cell_temp_warning = 0;
  warning_messages.min_cell_temp_warning = 0;

  //Screen message struct
  screen_messages.gate_driver_temp_value = 0;
  screen_messages.control_board_temp_value = 0;
  screen_messages.motor_temp_value = 0;
  screen_messages.DC_current_value = 0;
  screen_messages.DC_bus_voltage_value = 0;
  screen_messages.internal_voltage_value = 0;
  screen_messages.internal_states_value = 0;
  screen_messages.fault_codes_value = 0;
  screen_messages.RLEC_temp = 0;
  screen_messages.max_cell_voltage = 0;
  screen_messages.min_cell_voltage = 0;
  screen_messages.battery_percent = 0;
  screen_messages.min_cell_temp = 0;
  screen_messages.max_cell_temp = 0;
  screen_messages.motor_torque = 0;
  screen_messages.RMS_state = 0;
  screen_messages.last_RMS_state = 0;
}

/******************************************************************************
** WRITES 0 TO ALL OBJECTS ON THE SCREEN
** IF THIS IS NOT DONE, THE SCREEN REFUSES TO CHANGE VALUES OFF THE INITIAL VALUES
******************************************************************************/
void init_screen_objects(void) {
  //Main screen objects
  genie.WriteObject(GENIE_OBJ_ANGULAR_METER, CURRENT_METER_SCREEN_ID, 0);
  genie.WriteObject(GENIE_OBJ_ANGULAR_METER, MOTOR_TORQUE_METER_SCREEN_ID, 0);
  genie.WriteObject(GENIE_OBJ_TANK, BATTERY_METER_SCREEN_ID, 0);

  //Debug screen objects
  genie.WriteObject(GENIE_OBJ_LED_DIGITS, GATE_DRIVER_SCREEN_ID, 0);
  genie.WriteObject(GENIE_OBJ_LED_DIGITS, CONTROL_BOARD_SCREEN_ID, 0);
  genie.WriteObject(GENIE_OBJ_LED_DIGITS, MOTOR_TEMP_SCREEN_ID, 0);
  genie.WriteObject(GENIE_OBJ_LED_DIGITS, DC_CURRENT_SCREEN_ID, 0);
  genie.WriteObject(GENIE_OBJ_LED_DIGITS, DC_BUS_VOLTAGE_SCREEN_ID, 0);
  genie.WriteObject(GENIE_OBJ_LED_DIGITS, INTERNAL_VOLTAGE_SCREEN_ID, 0);
  genie.WriteObject(GENIE_OBJ_LED_DIGITS, RLEC_TEMP_SCREEN_ID, 0);
  genie.WriteObject(GENIE_OBJ_LED_DIGITS, MAX_CELL_VOLTAGE_SCREEN_ID, 0);
  genie.WriteObject(GENIE_OBJ_LED_DIGITS, MIN_CELL_VOLTAGE_SCREEN_ID, 0);
  genie.WriteObject(GENIE_OBJ_LED_DIGITS, MIN_CELL_TEMP_SCREEN_ID, 0);
  genie.WriteObject(GENIE_OBJ_LED_DIGITS, MAX_CELL_TEMP_SCREEN_ID, 0);

  //Warning screen objects
  genie.WriteObject(GENIE_OBJ_USER_LED, GATE_DRIVER_WARNING_SCREEN_ID, 0);
  genie.WriteObject(GENIE_OBJ_USER_LED, CONTROL_BOARD_WARNING_SCREEN_ID, 0);
  genie.WriteObject(GENIE_OBJ_USER_LED, WARNING_12V_VOLTAGE_SCREEN_ID, 0);
  genie.WriteObject(GENIE_OBJ_USER_LED, MAX_CELL_VOLTAGE_WARNING_SCREEN_ID, 0);
  genie.WriteObject(GENIE_OBJ_USER_LED, MIN_CELL_VOLTAGE_WARNING_SCREEN_ID, 0);
  genie.WriteObject(GENIE_OBJ_USER_LED, RLEC_WARNING_TEMP_SCREEN_ID, 0);
  genie.WriteObject(GENIE_OBJ_USER_LED, MAX_CELL_TEMP_WARNING_SCREEN_ID, 0);
  genie.WriteObject(GENIE_OBJ_USER_LED, MIN_CELL_TEMP_WARNING_SCREEN_ID, 0);
  genie.WriteObject(GENIE_OBJ_STRINGS, RMS_STATE_SCREEN_ID, 0);
}

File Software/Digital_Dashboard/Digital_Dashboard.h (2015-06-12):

// Digital Dash - Capstone 2015
// Sean Koppenhafer, Chad Thueson, Jaime Rodriguez, Rishal Dass and Noah Erickson
//
// Digital_Dashboard.h - Main header file for the program
//
// Uses due_can library from https://github.com/collin80/due_can

#ifndef DIGITAL_DASH_H
#define DIGITAL_DASH_H

#include <stdint.h>

#define CAN_FRAME_DATA_LEN 8

#define DISPLAY_SCREEN_OBJECTS
#define NO_WARNING 0
#define WARNING 1

/******************************************************************************
** MAIN SCREEN OBJECTS
******************************************************************************/
#define MOTOR_TORQUE_METER_SCREEN_ID 0x00
#define CURRENT_METER_SCREEN_ID 0x01
#define BATTERY_METER_SCREEN_ID 0x00
#define BMS_WARNING_IMAGE_SCREEN_ID 0x00
#define IMD_WARNING_IMAGE_SCREEN_ID 0x01
#define RMS_WARNING_IMAGE_SCREEN_ID 0x03
#define MAIN_TO_BMS_BUTTON_SCREEN_ID 0x01
#define MAIN_TO_RMS_BUTTON_SCREEN_ID 0x02
#define MAIN_TO_DEBUG_BUTTON_SCREEN_ID 0x03

/******************************************************************************
** DEBUG SCREEN OBJECTS
******************************************************************************/
//RMS
#define GATE_DRIVER_SCREEN_ID 		0x00
#define CONTROL_BOARD_SCREEN_ID         0x01
#define MOTOR_TORQUE_WARNING_SCREEN_ID  0x02
#define DC_CURRENT_SCREEN_ID		0x03
#define DC_BUS_VOLTAGE_SCREEN_ID	0x04
#define INTERNAL_VOLTAGE_SCREEN_ID	0x05
#define MOTOR_TEMP_SCREEN_ID 	        0x0B
#define RMS_STATE_SCREEN_ID             0x00

//BMS
#define RLEC_TEMP_SCREEN_ID		0x06
#define MAX_CELL_VOLTAGE_SCREEN_ID	0x07
#define MIN_CELL_VOLTAGE_SCREEN_ID	0x08
#define MIN_CELL_TEMP_SCREEN_ID		0x09
#define MAX_CELL_TEMP_SCREEN_ID		0x0A

#define DEBUG_TO_MAIN_BUTTON_SCREEN_ID 0x02  //Button to return to the main screen

/******************************************************************************
** WARNING SCREEN OBJECTS
******************************************************************************/
//RMS
#define GATE_DRIVER_WARNING_SCREEN_ID 0x00
#define CONTROL_BOARD_WARNING_SCREEN_ID 0x01
#define WARNING_12V_VOLTAGE_SCREEN_ID 0x02
#define RMS_TO_MAIN_BUTTON_SCREEN_ID 0x00

//BMS
#define MAX_CELL_VOLTAGE_WARNING_SCREEN_ID 0x03
#define MIN_CELL_VOLTAGE_WARNING_SCREEN_ID 0x04
#define RLEC_WARNING_TEMP_SCREEN_ID 0x05
#define MAX_CELL_TEMP_WARNING_SCREEN_ID 0x06
#define MIN_CELL_TEMP_WARNING_SCREEN_ID 0x07

#define BMS_TO_MAIN_BUTTON_SCREEN_ID 0x01  //Button to return to the main screen

/******************************************************************************
** WARNING MESSAGE THRESHOLDS
******************************************************************************/
//RMS
#define GATE_DRIVER_WARNING_TEMP 80
#define CONTROL_BOARD_WARNING_TEMP 80
#define WARNING_12V_VOLTAGE 11

//BMS
#define MAX_CELL_WARNING_VOLTAGE 420  //Actually 4.2V, just multipled by 100 for the screen
#define MIN_CELL_WARNING_VOLTAGE 320  //Actually 3.2V, just multipled by 100 for the screen
#define RLEC_WARNING_TEMP 60
#define MAX_CELL_WARNING_TEMP 40
#define MIN_CELL_WARNING_TEMP 0

//RMS STATES
#define START_STATE 0
#define INIT_STATE 1
#define ACTIVE_STATE 2
#define COMPLETE_STATE 3
#define WAIT_STATE 4
#define READY_STATE 5
#define RUNNING_STATE 6
#define BLINK_STATE 7
#define SHUTDOWN_STATE 8
#define POWER_STATE 9

/******************************************************************************
** ANALOG INPUT PINS
******************************************************************************/
#define IMD_BUTTON 3

/******************************************************************************
** STRUCT THAT CONTAINS FLAGS TO SIGNAL RMS AND BMS WARNINGS
** A VALUE OF 0 MEANS NO WARNING LIGHT. A VALUE OF 1 MEANS WARNING LIGHT IS ON
******************************************************************************/
typedef struct warning_msgs {         //Show warning when:
  bool gate_driver_temp_warning;      //Above 80C
  bool control_board_temp_warning;    //Above 80C
  bool voltage_12V_warning;           //Less than 11V for a few seconds
  bool max_cell_voltage_warning;      //Greater than 4.2V
  bool min_cell_voltage_warning;      //Less than 3.2V
  bool RLEC_temp_warning;             //Greater than 60C
  bool max_cell_temp_warning;         //Greater than 40C
  bool min_cell_temp_warning;         //Less than 0C
} warning_msgs;
  
/******************************************************************************
** THIS STRUCT CONTAINS THE DATA DISPLAYED ON THE SCREEN
******************************************************************************/
typedef struct screen_msgs {
  int gate_driver_temp_value;
  int control_board_temp_value;
  int motor_temp_value;
  int DC_current_value;
  int DC_bus_voltage_value;
  int internal_voltage_value;
  int internal_states_value;
  int fault_codes_value;
  int RLEC_temp;
  int max_cell_voltage;
  int min_cell_voltage;
  int battery_percent;
  int min_cell_temp;
  int max_cell_temp;
  int motor_torque;
  int RMS_state;
  int last_RMS_state;
} screen_msgs;
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

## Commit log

2015-01-17 Design Prototype A
    Prototype of mounting the screen
2015-01-17 Proposal Powerpoint
2015-01-25 Added the due_can library and added some test code for polling and interrupt driven CAN messaging
2015-01-27 Bill of Material Documentation
    List of parts ordered to date.
    [Bill of Materials.xlsx]
2015-01-28 Prices for components updated
    added unit price for due and tranceivers plus shipping
    [Bill of Materials.xlsx]
2015-01-28 Update
    Format
    [Bill of Materials.xlsx]
2015-01-31 Arduino Due Schematic
2015-01-31 BMS Can programming
    document of can messages from bms
2015-02-07 Added BMS CAN messages to CAN1
2015-02-07 Update
    BOM updated
    [Bill of Materials.xlsx]
2015-02-11 CAN1(BMS) tests added. Big endian conversion working correctly now. BMS values outputting correctly
    [CAN0.cpp, DIGITAL_DASH.ino]
2015-02-13 Prototype Board & Schematic
    This is the updated board and schematic for the prototype
    [Prototype_Board.brd, Prototype_Schematic.sch]
2015-02-22 Debug prints that work with interrupts
2015-02-28 Wiring Diagram
2015-03-02 Commit 100!
    Commit 100! Complete with weekly update presentation, some directory
    reorganization and report outline!
    [Bill of Materials.xlsx, RequirementSpecSpreadSheet.ods]
2015-03-14 jaime
    jhjhj
    [Arduino_DUE_X_V02d-2Layer.brd, Arduino_DUE_X_V02d-2Layer.sch]
2015-03-14 Enclosure Design
    Some prototype designs for the enclosure
2015-03-14 BMS code now working. All values displayed to screen
2015-03-14 Jaime
    Board
    [Custom_DUE.brd, Custom_DUE.sch]
2015-03-21 Bill of materials added to hardware
    [PrototypeBOM.xlsx]
2015-03-21 BOM update
    [PrototypeBOM.xlsx]
2015-03-21 RMS warning messages work and RMS symbol changes red on error
    [DIGITAL_DASH.ino]
2015-03-31 Arduino power supply and basic enclosure
    [Arduino5VPowerSupply.brd, Arduino5VPowerSupply.sch]
2015-04-05 Added pictures of prototype
2015-04-07 Hardware reorganization
    [Arduino_DUE_X_V02d-2Layer.brd, Arduino_DUE_X_V02d-2Layer.sch, InitialTransceivers.brd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]
2015-04-07 Hardware Reorg2
    [Arduino5VPowerSupply.brd, Arduino5VPowerSupply.sch, Arduino_DUE_X_V02d-2Layer.brd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]
2015-04-07 Schematic cleanup for Jaime
    [Arduino_DUE_X_V02d-2Layer.sch]
2015-04-11 Schematic Update
2015-04-11 New Pictures
    BMS removed pictures
2015-04-11 Enclosure Added
2015-04-25 Sending motor temp to screen with EVCU
2015-04-25 gate driver temp working with demo
2015-04-27 board pic uploaded
2015-04-29 Support for motor torque added into Demo sender
2015-05-05 Code that has motor_torque not working
    [CAN0.cpp, DIGITAL_DASH.ino]
2015-05-05 Atmega16u2 Breakout board upload
    [atmega16u2custom.brd, atmega16u2custom.sch]
2015-05-05 atmega16u2 breakout board update
    [atmega16u2custom.brd, atmega16u2custom.sch]
2015-05-09 Motor torque, gate driver temperature and IMD now work on the demo program/screen.
2015-05-09 ATMEGA16u2 Board Update
    [atmega16u2custom2.brd, atmega16u2custom2.sch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]
2015-05-09 The battery guage now works on the screen and in the demo. The current version of the demo should be totally done
2015-05-20 Updated atmega16 breakout board, and gerbers
    [atmega16u2custom2.sch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]
2015-05-26 BMS warning messages now make BMS symbol turn red.
2015-05-26 Fixed issue with screen locking up related to the battery. Also changed scale of the motor torque input values
2015-06-02 Picture update
    [Arduino_DUE_X_V02d-2Layer.sch]
2015-06-02 Update names and remove motor temp from demo
2015-06-03 Remove polling code that does not work
    [CAN0.cpp]
2015-06-03 Updates library
    Included 4d system arduino library
2015-06-03 Due and bare custom board
    Show difference in size between DUE and custom board
2015-06-03 Version of genieArduino Library used
    Library for 4dsystem screen to work with arduino
2015-06-04 Presentation and BOM update
    [PrototypeBOM.xlsx]
2015-06-05 Made final revisions to board
    added +5V and GND terminals for wire harness,
    fixed minor issues
    [Arduino_DUE_X_V02d-2Layer.brd, InitialTransceivers.brd, InitialTransceivers.sch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]
2015-06-10 Enclosure picture
    Updated enclosure picture
2015-06-10 Deutsch Connector Pinout Picture
2015-06-11 Added drawings for enclosure and dash
2015-06-12 Add additional LED for warning state and add motor temp object to info screen
2015-06-12 Change LED type
2015-06-13 updated gui
    added motor temp and added led to blink fault state
2015-06-13 final revision of gui
    updated guid to included motor torque and fixed the bms error

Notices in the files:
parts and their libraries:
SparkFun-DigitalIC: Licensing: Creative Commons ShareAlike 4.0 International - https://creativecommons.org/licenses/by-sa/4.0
